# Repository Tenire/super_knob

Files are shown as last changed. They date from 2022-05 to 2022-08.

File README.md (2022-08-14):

# Super knob

## 介绍
Super knob 是基于ESP32与无刷电机实现的超级旋钮，该项目基于国外开源项目：[smartknob](https://github.com/scottbez1/smartknob)

我将无刷电机的旋钮部分解耦出来，通过磁吸的方式搭配不同的底座，来实现各种应用场景，同时设计了一套协议用于旋钮与底座的交互，可实现针对不同场景带来不同的触感体验，甚至可以在同一个场景的不同操作下模拟不同的触感和阻尼反馈。类似于智能手机中线性马达对于不同应用或页面的机械触感模拟。

同时磁吸的灵感来源于大疆的Action2 方块相机，啪，即可将旋钮与不同外设进行磁吸配对，待开发稳定后，计划用CNC加工金属的外壳，来配合磁吸达到最舒服的体验。

例如：当同一个旋钮组件，磁吸到物联网中控的底座上面，自动弹出对应的UI界面，同时可以控制智能家具，且在控制台灯亮度和空调温度的时候，会带来不同的旋钮触感反馈。

例如：当同一个旋钮组件，磁吸到PC旋钮底座上面，即可变身为PC的超级旋钮，可以用他做翻页、快捷键、切换应用、调节音量和亮度，只要你喜欢，都可以分别为这几个功能配置不同的阻尼反馈。

将旋钮部分解耦开来，搭配不同的底座，即可实现控制万物，且触感与阻尼感各不相同，这是普通的机械旋钮不能带来的！

## 目录结构

1.Firmware   固件代码 平台为platformIO

2.Hardware  硬件PCB相关文件

3.Model  三维模型文件，软件为SolidWorks

4.Super Knob Submodules 超级旋钮底座子模块，或许会增加更多

Docs 图片资源

Tools 字库等工具

## 设计草图

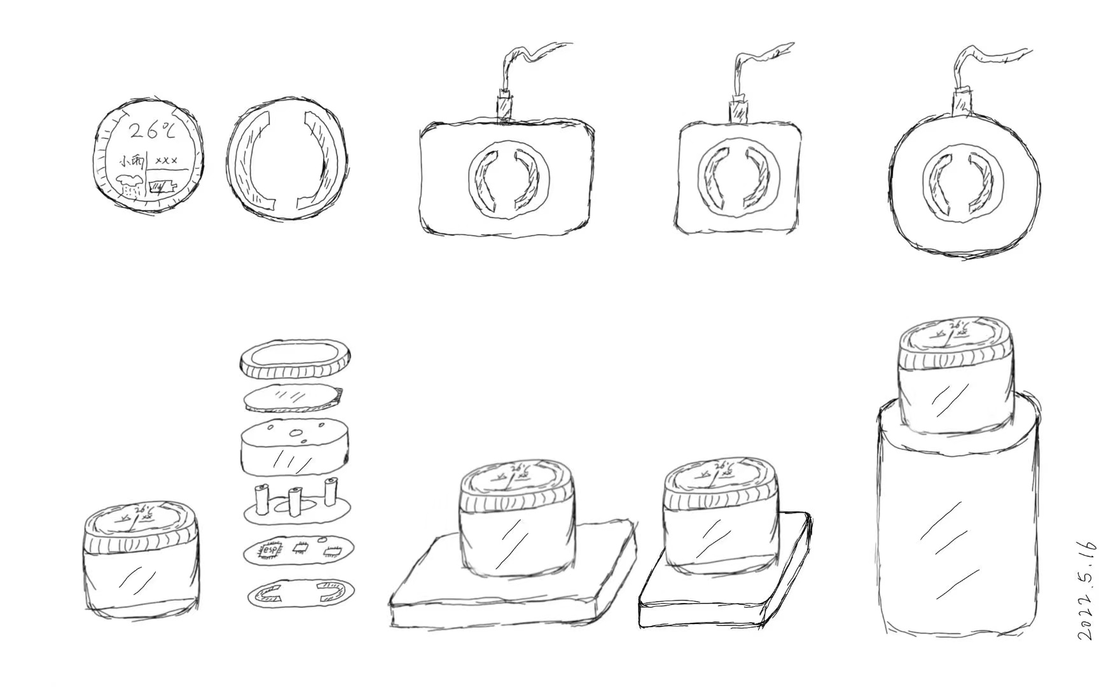
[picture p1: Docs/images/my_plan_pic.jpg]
my_plan_pic


## 功能架构

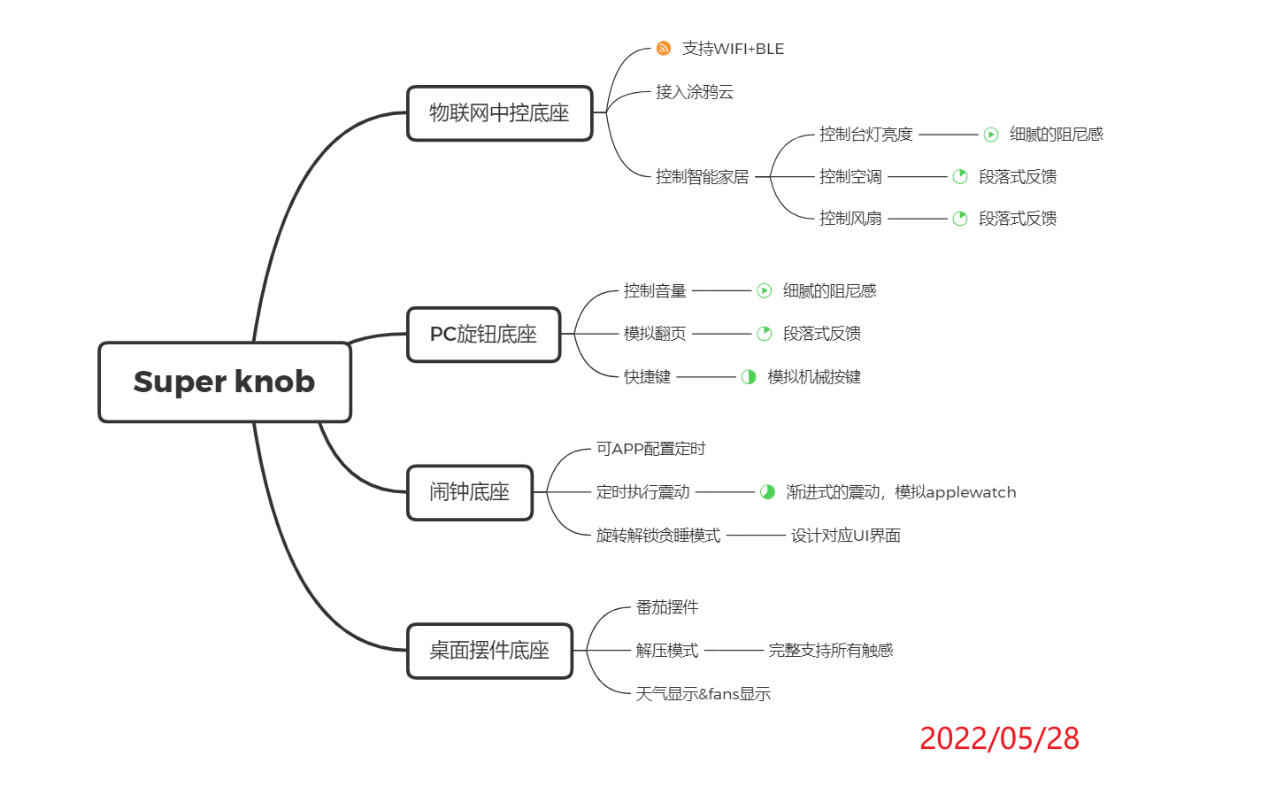
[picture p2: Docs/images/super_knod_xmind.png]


## UI界面演示

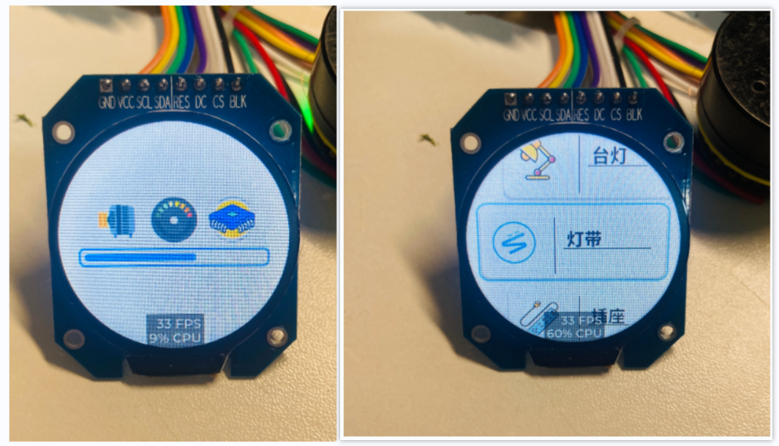
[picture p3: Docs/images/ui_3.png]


## 3D模型（初版）

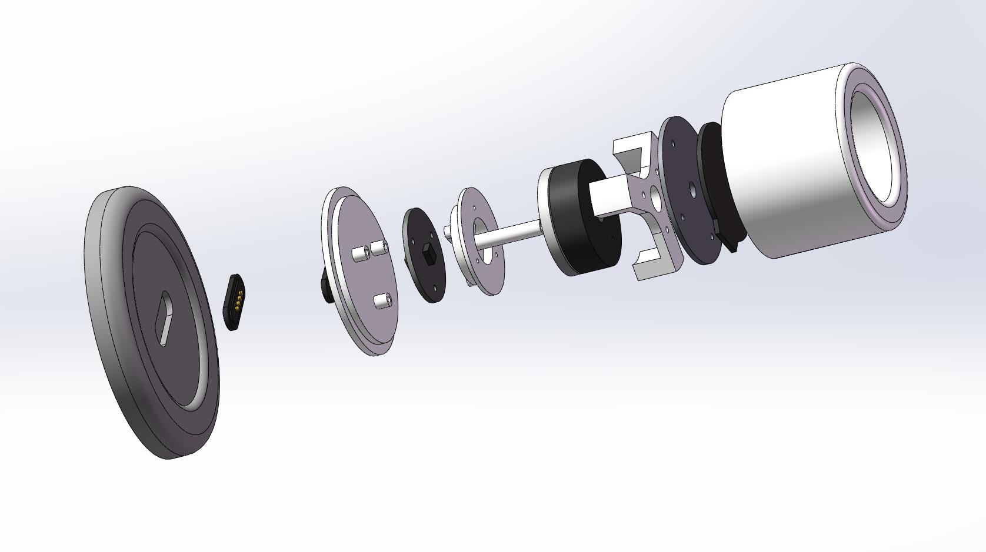
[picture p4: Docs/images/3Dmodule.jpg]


改进版本：

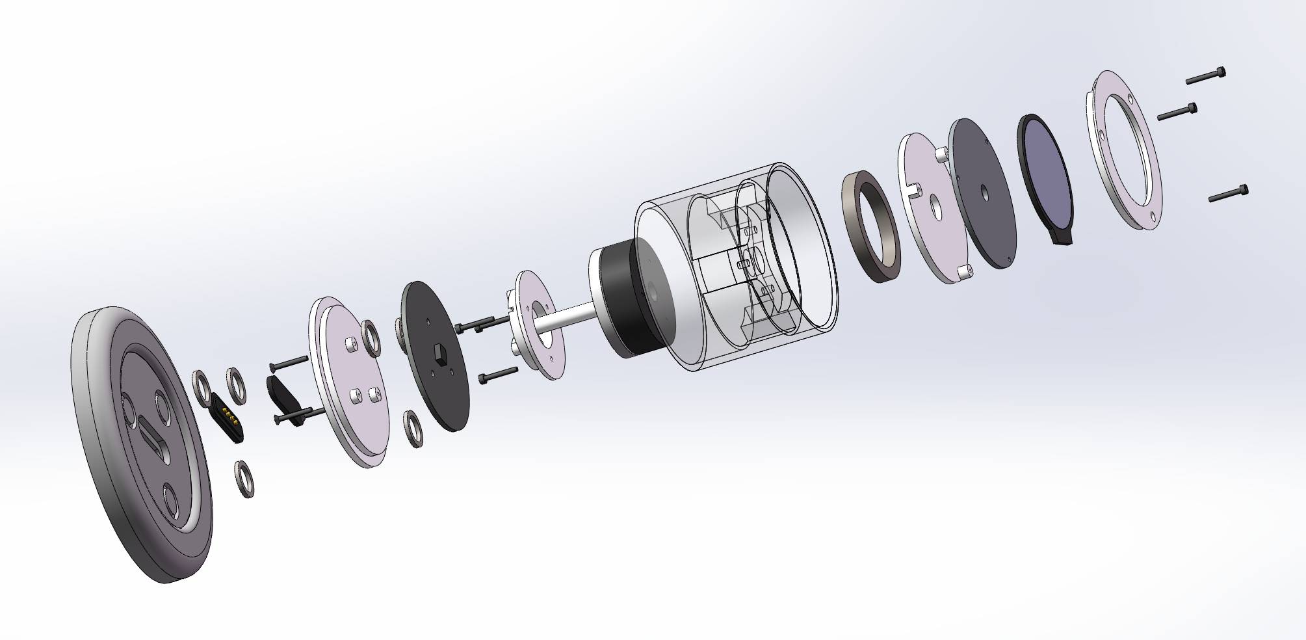
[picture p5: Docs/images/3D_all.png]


兼容2804电机：

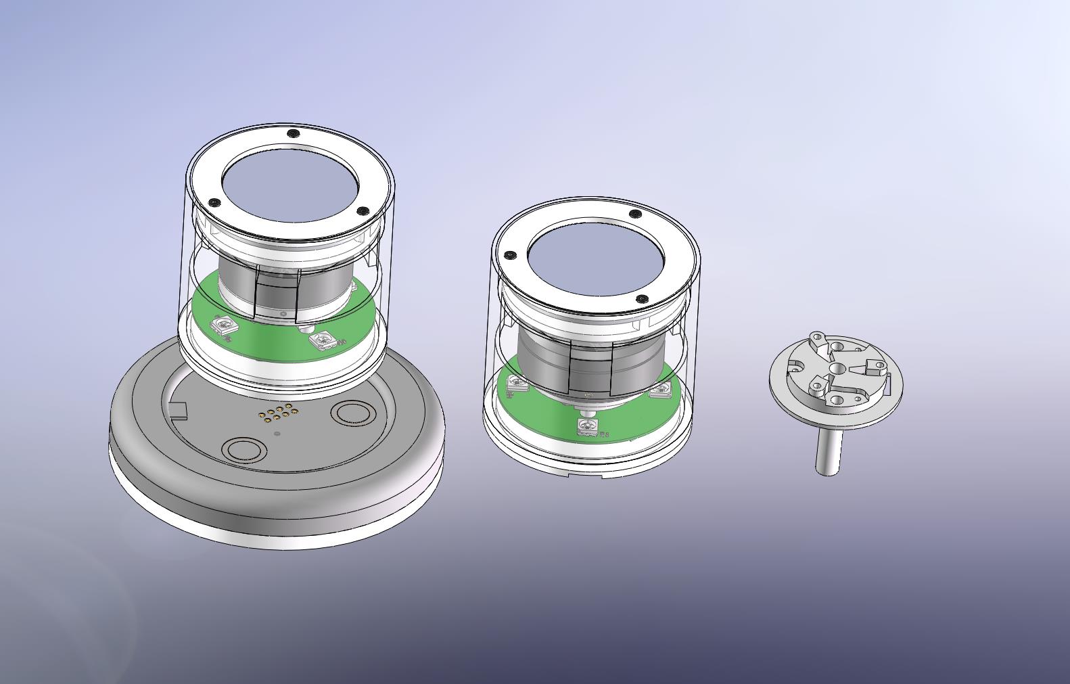
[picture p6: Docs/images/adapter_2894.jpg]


# Super knob Lite

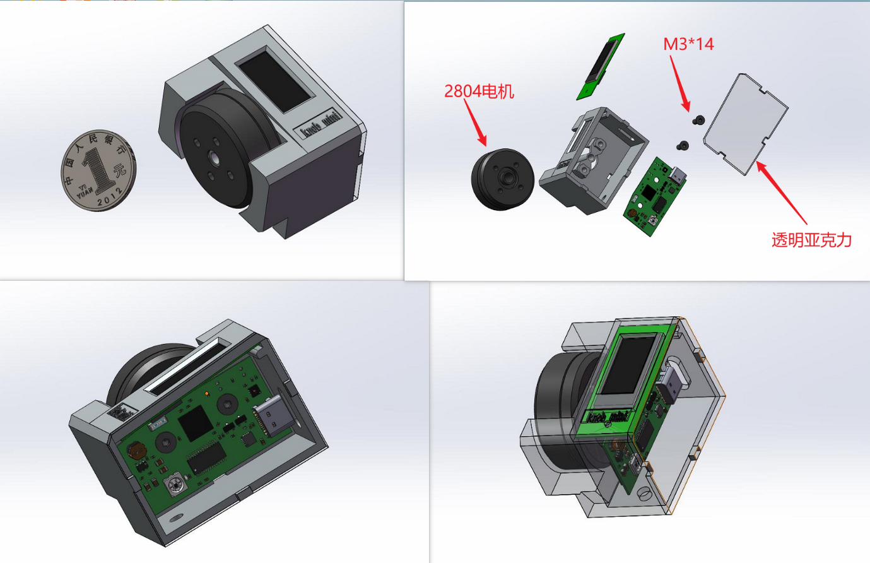
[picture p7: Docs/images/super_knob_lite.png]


## 介绍

Super knob Lite 是基于Super knob的版本进行了优化缩小的 迷你版本，整体外观是参考稚晖君键盘左侧拓展模块设计而来，当天看到稚晖君发布视频后，我拿起游标卡尺和电机就开始了设计，几个小时完成并连夜画PCB验证，并且一次打样通过！致敬偶像，一直激励着我们学习新的东西。

固件代码请切换至 develop/super_knob_lite分支 我还在持续优化ing

`git fetch`

`git pull`

`git checkout  develop/super_knob_lite`

## 电机选型

该项目已适配2804电机，能正常买到，目前看来供货充足，同时也需要配一个径向磁铁磁环

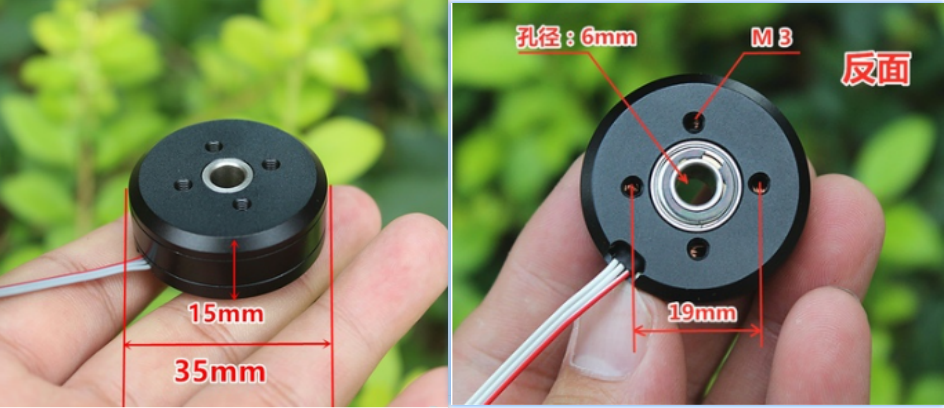
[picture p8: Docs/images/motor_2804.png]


2804电机淘宝链接：[链接地址](https://item.taobao.com/item.htm?spm=a1z09.2.0.0.10d92e8d2bksqC&id=656316178382&_u=22es8v8793db)

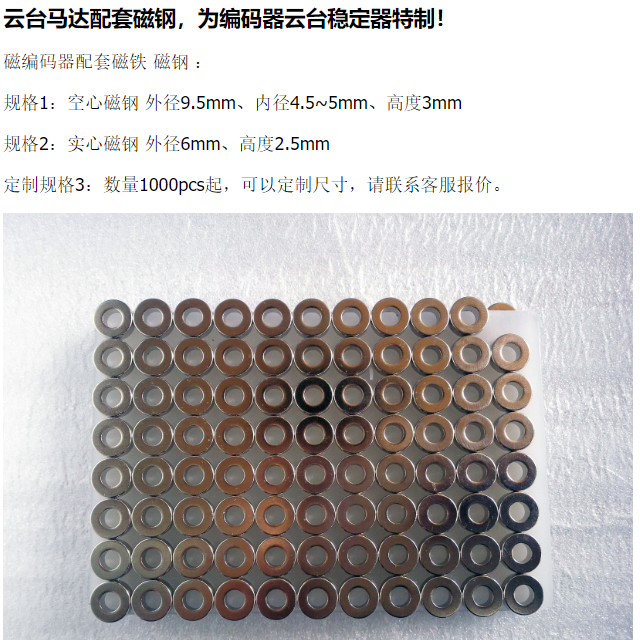
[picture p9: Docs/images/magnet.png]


径向磁铁淘宝链接：[链接地址](https://item.taobao.com/item.htm?spm=a1z09.2.0.0.1a622e8d9RsXzr&id=547732283636&_u=e2es8v87891e)

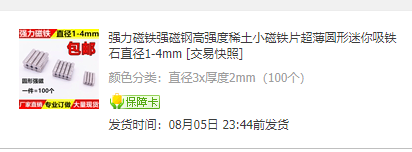
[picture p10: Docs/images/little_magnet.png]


亚克力外壳磁吸 小磁铁(直径3 厚度2)：[链接地址](https://item.taobao.com/item.htm?spm=a1z09.2.0.0.1a622e8d9RsXzr&id=536670444365&_u=e2es8v878c66)

关于左侧的按键，其实是通过ESP32的TouchGPIO来实现的，从PCB引出GPIO贯穿电机到达左侧，手指触摸即可得到相应反馈，同时电机也会模拟震动，来达到机械按键的效果。

## 视频演示：

功能演示：
https://www.bilibili.com/video/BV1GG4y1q7WF

详细介绍与开发指导：
https://www.bilibili.com/video/BV1BB4y157gH

# 鸣谢

https://github.com/peng-zhihui/HelloWord-Keyboard

https://github.com/scottbez1/smartknob

https://github.com/ToanTech/Deng-s-foc-controller

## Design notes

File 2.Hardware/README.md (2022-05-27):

<!--
 * @Descripttion: 
 * @version: 
 * @Author: congsir
 * @Date: 2022-05-26 23:58:26
 * @LastEditors: 
 * @LastEditTime: 2022-05-27 23:52:37
-->
# Super knob

#### 介绍
uper knob 是基于ESP32与无刷电机实现的超级旋钮，该项目基于国外开源项目：[smartknob](https://github.com/scottbez1/smartknob)

my_plan_pic

ui_1

#### 软件架构

软件架构说明

#### 安装教程

1.  xxxx
2.  xxxx
3.  xxxx

#### 使用说明

1.  xxxx
2.  xxxx
3.  xxxx

#### 参与贡献

1.  Fork 本仓库
2.  新建 Feat_xxx 分支
3.  提交代码
4.  新建 Pull Request

#### 特技

1.  使用 Readme\_XXX.md 来支持不同的语言，例如 Readme\_en.md, Readme\_zh.md
2.  Gitee 官方博客 [blog.gitee.com](https://blog.gitee.com)
3.  你可以 [https://gitee.com/explore](https://gitee.com/explore) 这个地址来了解 Gitee 上的优秀开源项目
4.  [GVP](https://gitee.com/gvp) 全称是 Gitee 最有价值开源项目，是综合评定出的优秀开源项目
5.  Gitee 官方提供的使用手册 [https://gitee.com/help](https://gitee.com/help)
6.  Gitee 封面人物是一档用来展示 Gitee 会员风采的栏目 [https://gitee.com/gitee-stars/](https://gitee.com/gitee-stars/)

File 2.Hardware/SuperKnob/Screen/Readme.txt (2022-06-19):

注：三个触摸按键的金属化过孔需要开窗。

嘉立创下单Gerber文件才能按照设计文件选择金属化过孔是否开窗。

请屏幕的PCB板按照Gerber在嘉立创下单。

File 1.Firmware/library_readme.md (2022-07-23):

<!--
 * @Descripttion: 
 * @version: 
 * @Author: congsir
 * @Date: 2022-05-22 23:52:31
 * @LastEditors: wenzheng 565402462@qq.com
 * @LastEditTime: 2022-07-23 16:10:56
-->
## 依赖库的配置与注意事项

simple FOC 的版本2.2.1→ ESP32版本4.1.0！！！！！！！！

1 TFT_eSPI/User_Setup.h

2 lvgl/lv_conf.h

---

TFT_eSPI/User_Setup.h
```

#define GC9A01_DRIVER

//#define ST7789_DRIVER  
#define TFT_WIDTH  240
#define TFT_HEIGHT 240

#ifdef ESP32C3_ENABLE
    #define TFT_MOSI 3 // In some display driver board, it might be written as "SDA" and so on.15
    #define TFT_SCLK 2 //14
    #define TFT_CS   7  // Chip select control pin
    #define TFT_DC   6  // Data Command control pin
    #define TFT_RST  10  // Reset pin (could connect to Arduino RESET pin)
    #define TFT_BL   12  // LED back-light
#else
    #define TFT_MOSI 13 // In some display driver board, it might be written as "SDA" and so on.15
    #define TFT_SCLK 14 //14
    #define TFT_CS   15  // Chip select control pin
    #define TFT_DC   27  // Data Command control pin
    #define TFT_RST  2  // Reset pin (could connect to Arduino RESET pin)
    #define TFT_BL   12  // LED back-light
    #define ESP32_DMA
#endif // ESP32C3_ENABLE

#define LOAD_GLCD   // Font 1. Original Adafruit 8 pixel font needs ~1820 bytes in FLASH
// #define LOAD_FONT2  // Font 2. Small 16 pixel high font, needs ~3534 bytes in FLASH, 96 characters
// #define LOAD_FONT4  // Font 4. Medium 26 pixel high font, needs ~5848 bytes in FLASH, 96 characters
// #define LOAD_FONT6  // Font 6. Large 48 pixel font, needs ~2666 bytes in FLASH, only characters 1234567890:-.apm
// #define LOAD_FONT7  // Font 7. 7 segment 48 pixel font, needs ~2438 bytes in FLASH, only characters 1234567890:-.
// #define LOAD_FONT8  // Font 8. Large 75 pixel font needs ~3256 bytes in FLASH, only characters 1234567890:-.
// #define LOAD_GFXFF  // FreeFonts. Include access to the 48 Adafruit_GFX free fonts FF1 to FF48 and custom fonts

//#define SMOOTH_FONT
#define SPI_FREQUENCY  80000000
#define SPI_READ_FREQUENCY  8000000
//#define SPI_TOUCH_FREQUENCY  2500000 

//https://www.bilibili.com/read/cv13270143?spm_id_from=333.999.0.0

```
lvgl/lv_conf.h

```
/**
 * @file lv_conf.h
 * Configuration file for v8.2.0
 */

/*
 * Copy this file as `lv_conf.h`
 * 1. simply next to the `lvgl` folder
 * 2. or any other places and
 *    - define `LV_CONF_INCLUDE_SIMPLE`
 *    - add the path as include path
 */

/* clang-format off */
#if 1 /*Set it to "1" to enable content*/

#ifndef LV_CONF_H
#define LV_CONF_H

#include <stdint.h>

/*====================
   COLOR SETTINGS
 *====================*/

/*Color depth: 1 (1 byte per pixel), 8 (RGB332), 16 (RGB565), 32 (ARGB8888)*/
#define LV_COLOR_DEPTH 16

/*Swap the 2 bytes of RGB565 color. Useful if the display has an 8-bit interface (e.g. SPI)*/
#define LV_COLOR_16_SWAP 0

/*Enable more complex drawing routines to manage screens transparency.
 *Can be used if the UI is above another layer, e.g. an OSD menu or video player.
 *Requires `LV_COLOR_DEPTH = 32` colors and the screen's `bg_opa` should be set to non LV_OPA_COVER value*/
#define LV_COLOR_SCREEN_TRANSP 0

/* Adjust color mix functions rounding. GPUs might calculate color mix (blending) differently.
 * 0: round down, 64: round up from x.75, 128: round up from half, 192: round up from x.25, 254: round up */
#define LV_COLOR_MIX_ROUND_OFS (LV_COLOR_DEPTH == 32 ? 0: 128)

/*Images pixels with this color will not be drawn if they are chroma keyed)*/
#define LV_COLOR_CHROMA_KEY lv_color_hex(0x00ff00)         /*pure green*/

/*=========================
   MEMORY SETTINGS
 *=========================*/

/*1: use custom malloc/free, 0: use the built-in `lv_mem_alloc()` and `lv_mem_free()`*/
#define LV_MEM_CUSTOM 0
#if LV_MEM_CUSTOM == 0
    /*Size of the memory available for `lv_mem_alloc()` in bytes (>= 2kB)*/
    #define LV_MEM_SIZE (64U * 1024U)          /*[bytes]*/

    /*Set an address for the memory pool instead of allocating it as a normal array. Can be in external SRAM too.*/
    #define LV_MEM_ADR 0     /*0: unused*/
    /*Instead of an address give a memory allocator that will be called to get a memory pool for LVGL. E.g. my_malloc*/
    #if LV_MEM_ADR == 0
        //#define LV_MEM_POOL_INCLUDE your_alloc_library  /* Uncomment if using an external allocator*/
        //#define LV_MEM_POOL_ALLOC   your_alloc          /* Uncomment if using an external allocator*/
    #endif

#else       /*LV_MEM_CUSTOM*/
    #define LV_MEM_CUSTOM_INCLUDE <stdlib.h>   /*Header for the dynamic memory function*/
    #define LV_MEM_CUSTOM_ALLOC   malloc
    #define LV_MEM_CUSTOM_FREE    free
    #define LV_MEM_CUSTOM_REALLOC realloc
#endif     /*LV_MEM_CUSTOM*/

/*Number of the intermediate memory buffer used during rendering and other internal processing mechanisms.
 *You will see an error log message if there wasn't enough buffers. */
#define LV_MEM_BUF_MAX_NUM 16

/*Use the standard `memcpy` and `memset` instead of LVGL's own functions. (Might or might not be faster).*/
#define LV_MEMCPY_MEMSET_STD 0

/*====================
   HAL SETTINGS
 *====================*/

/*Default display refresh period. LVG will redraw changed areas with this period time*/
#define LV_DISP_DEF_REFR_PERIOD 30      /*[ms]*/

/*Input device read period in milliseconds*/
#define LV_INDEV_DEF_READ_PERIOD 30     /*[ms]*/

/*Use a custom tick source that tells the elapsed time in milliseconds.
 *It removes the need to manually update the tick with `lv_tick_inc()`)*/
#define LV_TICK_CUSTOM 1
#if LV_TICK_CUSTOM
    #define LV_TICK_CUSTOM_INCLUDE "Arduino.h"         /*Header for the system time function*/
    #define LV_TICK_CUSTOM_SYS_TIME_EXPR (millis())    /*Expression evaluating to current system time in ms*/
#endif   /*LV_TICK_CUSTOM*/

/*Default Dot Per Inch. Used to initialize default sizes such as widgets sized, style paddings.
 *(Not so important, you can adjust it to modify default sizes and spaces)*/
#define LV_DPI_DEF 130     /*[px/inch]*/

/*=======================
 * FEATURE CONFIGURATION
 *=======================*/

/*-------------
 * Drawing
 *-----------*/

/*Enable complex draw engine.
 *Required to draw shadow, gradient, rounded corners, circles, arc, skew lines, image transformations or any masks*/
#define LV_DRAW_COMPLEX 1
#if LV_DRAW_COMPLEX != 0

    /*Allow buffering some shadow calculation.
    *LV_SHADOW_CACHE_SIZE is the max. shadow size to buffer, where shadow size is `shadow_width + radius`
    *Caching has LV_SHADOW_CACHE_SIZE^2 RAM cost*/
    #define LV_SHADOW_CACHE_SIZE 0

    /* Set number of maximally cached circle data.
    * The circumference of 1/4 circle are saved for anti-aliasing
    * radius * 4 bytes are used per circle (the most often used radiuses are saved)
    * 0: to disable caching */
    #define LV_CIRCLE_CACHE_SIZE 4
#endif /*LV_DRAW_COMPLEX*/

/*Default image cache size. Image caching keeps the images opened.
 *If only the built-in image formats are used there is no real advantage of caching. (I.e. if no new image decoder is added)
 *With complex image decoders (e.g. PNG or JPG) caching can save the continuous open/decode of images.
 *However the opened images might consume additional RAM.
 *0: to disable caching*/
#define LV_IMG_CACHE_DEF_SIZE   0

/*Number of stops allowed per gradient. Increase this to allow more stops.
 *This adds (sizeof(lv_color_t) + 1) bytes per additional stop*/
#define LV_GRADIENT_MAX_STOPS       2

/*Default gradient buffer size.
 *When LVGL calculates the gradient "maps" it can save them into a cache to avoid calculating them again.
 *LV_GRAD_CACHE_DEF_SIZE sets the size of this cache in bytes.
 *If the cache is too small the map will be allocated only while it's required for the drawing.
 *0 mean no caching.*/
#define LV_GRAD_CACHE_DEF_SIZE      0

/*Allow dithering the gradients (to achieve visual smooth color gradients on limited color depth display)
 *LV_DITHER_GRADIENT implies allocating one or two more lines of the object's rendering surface
 *The increase in memory consumption is (32 bits * object width) plus 24 bits * object width if using error diffusion */
#define LV_DITHER_GRADIENT      0
#if LV_DITHER_GRADIENT
    /*Add support for error diffusion dithering.
     *Error diffusion dithering gets a much better visual result, but implies more CPU consumption and memory when drawing.
     *The increase in memory consumption is (24 bits * object's width)*/
    #define LV_DITHER_ERROR_DIFFUSION   0
#endif

/*Maximum buffer size to allocate for rotation.
 *Only used if software rotation is enabled in the display driver.*/
#define LV_DISP_ROT_MAX_BUF (10*1024)

/*-------------
 * GPU
 *-----------*/

/*Use STM32's DMA2D (aka Chrom Art) GPU*/
#define LV_USE_GPU_STM32_DMA2D 0
#if LV_USE_GPU_STM32_DMA2D
    /*Must be defined to include path of CMSIS header of target processor
    e.g. "stm32f769xx.h" or "stm32f429xx.h"*/
    #define LV_GPU_DMA2D_CMSIS_INCLUDE
#endif

/*Use NXP's PXP GPU iMX RTxxx platforms*/
#define LV_USE_GPU_NXP_PXP 0
#if LV_USE_GPU_NXP_PXP
    /*1: Add default bare metal and FreeRTOS interrupt handling routines for PXP (lv_gpu_nxp_pxp_osa.c)
    *   and call lv_gpu_nxp_pxp_init() automatically during lv_init(). Note that symbol SDK_OS_FREE_RTOS
    *   has to be defined in order to use FreeRTOS OSA, otherwise bare-metal implementation is selected.
    *0: lv_gpu_nxp_pxp_init() has to be called manually before lv_init()
    */
    #define LV_USE_GPU_NXP_PXP_AUTO_INIT 0
#endif

/*Use NXP's VG-Lite GPU iMX RTxxx platforms*/
#define LV_USE_GPU_NXP_VG_LITE 0

/*Use SDL renderer API*/
#define LV_USE_GPU_SDL 0
#if LV_USE_GPU_SDL
    #define LV_GPU_SDL_INCLUDE_PATH <SDL2/SDL.h>
    /*Texture cache size, 8MB by default*/
    #define LV_GPU_SDL_LRU_SIZE (1024 * 1024 * 8)
    /*Custom blend mode for mask drawing, disable if you need to link with older SDL2 lib*/
    #define LV_GPU_SDL_CUSTOM_BLEND_MODE (SDL_VERSION_ATLEAST(2, 0, 6))
#endif

/*-------------
 * Logging
 *-----------*/

/*Enable the log module*/
#define LV_USE_LOG 0
#if LV_USE_LOG

    /*How important log should be added:
    *LV_LOG_LEVEL_TRACE       A lot of logs to give detailed information
    *LV_LOG_LEVEL_INFO        Log important events
    *LV_LOG_LEVEL_WARN        Log if something unwanted happened but didn't cause a problem
    *LV_LOG_LEVEL_ERROR       Only critical issue, when the system may fail
    *LV_LOG_LEVEL_USER        Only logs added by the user
    *LV_LOG_LEVEL_NONE        Do not log anything*/
    #define LV_LOG_LEVEL LV_LOG_LEVEL_WARN

    /*1: Print the log with 'printf';
    *0: User need to register a callback with `lv_log_register_print_cb()`*/
    #define LV_LOG_PRINTF 0

    /*Enable/disable LV_LOG_TRACE in modules that produces a huge number of logs*/
    #define LV_LOG_TRACE_MEM        1
    #define LV_LOG_TRACE_TIMER      1
    #define LV_LOG_TRACE_INDEV      1
    #define LV_LOG_TRACE_DISP_REFR  1
    #define LV_LOG_TRACE_EVENT      1
    #define LV_LOG_TRACE_OBJ_CREATE 1
    #define LV_LOG_TRACE_LAYOUT     1
    #define LV_LOG_TRACE_ANIM       1

#endif  /*LV_USE_LOG*/

/*-------------
 * Asserts
 *-----------*/

/*Enable asserts if an operation is failed or an invalid data is found.
 *If LV_USE_LOG is enabled an error message will be printed on failure*/
#define LV_USE_ASSERT_NULL          1   /*Check if the parameter is NULL. (Very fast, recommended)*/
#define LV_USE_ASSERT_MALLOC        1   /*Checks is the memory is successfully allocated or no. (Very fast, recommended)*/
#define LV_USE_ASSERT_STYLE         0   /*Check if the styles are properly initialized. (Very fast, recommended)*/
#define LV_USE_ASSERT_MEM_INTEGRITY 0   /*Check the integrity of `lv_mem` after critical operations. (Slow)*/
#define LV_USE_ASSERT_OBJ           0   /*Check the object's type and existence (e.g. not deleted). (Slow)*/

/*Add a custom handler when assert happens e.g. to restart the MCU*/
#define LV_ASSERT_HANDLER_INCLUDE <stdint.h>
#define LV_ASSERT_HANDLER while(1);   /*Halt by default*/

/*-------------
 * Others
 *-----------*/

/*1: Show CPU usage and FPS count*/
#define LV_USE_PERF_MONITOR 1
#if LV_USE_PERF_MONITOR
    #define LV_USE_PERF_MONITOR_POS LV_ALIGN_BOTTOM_MID
#endif

/*1: Show the used memory and the memory fragmentation
 * Requires LV_MEM_CUSTOM = 0*/
#define LV_USE_MEM_MONITOR 0
#if LV_USE_MEM_MONITOR
    #define LV_USE_MEM_MONITOR_POS LV_ALIGN_BOTTOM_LEFT
#endif

/*1: Draw random colored rectangles over the redrawn areas*/
#define LV_USE_REFR_DEBUG 0

/*Change the built in (v)snprintf functions*/
#define LV_SPRINTF_CUSTOM 0
#if LV_SPRINTF_CUSTOM
    #define LV_SPRINTF_INCLUDE <stdio.h>
    #define lv_snprintf  snprintf
    #define lv_vsnprintf vsnprintf
#else   /*LV_SPRINTF_CUSTOM*/
    #define LV_SPRINTF_USE_FLOAT 0
#endif  /*LV_SPRINTF_CUSTOM*/

#define LV_USE_USER_DATA 1

/*Garbage Collector settings
 *Used if lvgl is bound to higher level language and the memory is managed by that language*/
#define LV_ENABLE_GC 0
#if LV_ENABLE_GC != 0
    #define LV_GC_INCLUDE "gc.h"                           /*Include Garbage Collector related things*/
#endif /*LV_ENABLE_GC*/

/*=====================
 *  COMPILER SETTINGS
 *====================*/

/*For big endian systems set to 1*/
#define LV_BIG_ENDIAN_SYSTEM 0

/*Define a custom attribute to `lv_tick_inc` function*/
#define LV_ATTRIBUTE_TICK_INC

/*Define a custom attribute to `lv_timer_handler` function*/
#define LV_ATTRIBUTE_TIMER_HANDLER

/*Define a custom attribute to `lv_disp_flush_ready` function*/
#define LV_ATTRIBUTE_FLUSH_READY

/*Required alignment size for buffers*/
#define LV_ATTRIBUTE_MEM_ALIGN_SIZE 1

/*Will be added where memories needs to be aligned (with -Os data might not be aligned to boundary by default).
 * E.g. __attribute__((aligned(4)))*/
#define LV_ATTRIBUTE_MEM_ALIGN

/*Attribute to mark large constant arrays for example font's bitmaps*/
#define LV_ATTRIBUTE_LARGE_CONST

/*Compiler prefix for a big array declaration in RAM*/
#define LV_ATTRIBUTE_LARGE_RAM_ARRAY

/*Place performance critical functions into a faster memory (e.g RAM)*/
#define LV_ATTRIBUTE_FAST_MEM

/*Prefix variables that are used in GPU accelerated operations, often these need to be placed in RAM sections that are DMA accessible*/
#define LV_ATTRIBUTE_DMA

/*Export integer constant to binding. This macro is used with constants in the form of LV_<CONST> that
 *should also appear on LVGL binding API such as Micropython.*/
#define LV_EXPORT_CONST_INT(int_value) struct _silence_gcc_warning /*The default value just prevents GCC warning*/

/*Extend the default -32k..32k coordinate range to -4M..4M by using int32_t for coordinates instead of int16_t*/
#define LV_USE_LARGE_COORD 0

/*==================
 *   FONT USAGE
 *===================*/

/*Montserrat fonts with ASCII range and some symbols using bpp = 4
 *https://fonts.google.com/specimen/Montserrat*/
#define LV_FONT_MONTSERRAT_8  0
#define LV_FONT_MONTSERRAT_10 0
#define LV_FONT_MONTSERRAT_12 0
#define LV_FONT_MONTSERRAT_14 1
#define LV_FONT_MONTSERRAT_16 0
#define LV_FONT_MONTSERRAT_18 0
#define LV_FONT_MONTSERRAT_20 0
#define LV_FONT_MONTSERRAT_22 0
#define LV_FONT_MONTSERRAT_24 0
#define LV_FONT_MONTSERRAT_26 0
#define LV_FONT_MONTSERRAT_28 0
#define LV_FONT_MONTSERRAT_30 0
#define LV_FONT_MONTSERRAT_32 0
#define LV_FONT_MONTSERRAT_34 0
#define LV_FONT_MONTSERRAT_36 0
#define LV_FONT_MONTSERRAT_38 0
#define LV_FONT_MONTSERRAT_40 0
#define LV_FONT_MONTSERRAT_42 0
#define LV_FONT_MONTSERRAT_44 0
#define LV_FONT_MONTSERRAT_46 0
#define LV_FONT_MONTSERRAT_48 0

/*Demonstrate special features*/
#define LV_FONT_MONTSERRAT_12_SUBPX      0
#define LV_FONT_MONTSERRAT_28_COMPRESSED 0  /*bpp = 3*/
#define LV_FONT_DEJAVU_16_PERSIAN_HEBREW 0  /*Hebrew, Arabic, Persian letters and all their forms*/
#define LV_FONT_SIMSUN_16_CJK            0  /*1000 most common CJK radicals*/

/*Pixel perfect monospace fonts*/
#define LV_FONT_UNSCII_8  0
#define LV_FONT_UNSCII_16 0

/*Optionally declare custom fonts here.
 *You can use these fonts as default font too and they will be available globally.
 *E.g. #define LV_FONT_CUSTOM_DECLARE   LV_FONT_DECLARE(my_font_1) LV_FONT_DECLARE(my_font_2)*/
#define LV_FONT_CUSTOM_DECLARE

/*Always set a default font*/
#define LV_FONT_DEFAULT &lv_font_montserrat_14

/*Enable handling large font and/or fonts with a lot of characters.
 *The limit depends on the font size, font face and bpp.
 *Compiler error will be triggered if a font needs it.*/
#define LV_FONT_FMT_TXT_LARGE 0

/*Enables/disables support for compressed fonts.*/
#define LV_USE_FONT_COMPRESSED 0

/*Enable subpixel rendering*/
#define LV_USE_FONT_SUBPX 0
#if LV_USE_FONT_SUBPX
    /*Set the pixel order of the display. Physical order of RGB channels. Doesn't matter with "normal" fonts.*/
    #define LV_FONT_SUBPX_BGR 0  /*0: RGB; 1:BGR order*/
#endif

/*=================
 *  TEXT SETTINGS
 *=================*/

/**
 * Select a character encoding for strings.
 * Your IDE or editor should have the same character encoding
 * - LV_TXT_ENC_UTF8
 * - LV_TXT_ENC_ASCII
 */
#define LV_TXT_ENC LV_TXT_ENC_UTF8

/*Can break (wrap) texts on these chars*/
#define LV_TXT_BREAK_CHARS " ,.;:-_"

/*If a word is at least this long, will break wherever "prettiest"
 *To disable, set to a value <= 0*/
#define LV_TXT_LINE_BREAK_LONG_LEN 0

/*Minimum number of characters in a long word to put on a line before a break.
 *Depends on LV_TXT_LINE_BREAK_LONG_LEN.*/
#define LV_TXT_LINE_BREAK_LONG_PRE_MIN_LEN 3

/*Minimum number of characters in a long word to put on a line after a break.
 *Depends on LV_TXT_LINE_BREAK_LONG_LEN.*/
#define LV_TXT_LINE_BREAK_LONG_POST_MIN_LEN 3

/*The control character to use for signalling text recoloring.*/
#define LV_TXT_COLOR_CMD "#"

/*Support bidirectional texts. Allows mixing Left-to-Right and Right-to-Left texts.
 *The direction will be processed according to the Unicode Bidirectional Algorithm:
 *https://www.w3.org/International/articles/inline-bidi-markup/uba-basics*/
#define LV_USE_BIDI 0
#if LV_USE_BIDI
    /*Set the default direction. Supported values:
    *`LV_BASE_DIR_LTR` Left-to-Right
    *`LV_BASE_DIR_RTL` Right-to-Left
    *`LV_BASE_DIR_AUTO` detect texts base direction*/
    #define LV_BIDI_BASE_DIR_DEF LV_BASE_DIR_AUTO
#endif

/*Enable Arabic/Persian processing
 *In these languages characters should be replaced with an other form based on their position in the text*/
#define LV_USE_ARABIC_PERSIAN_CHARS 0

/*==================
 *  WIDGET USAGE
 *================*/

/*Documentation of the widgets: https://docs.lvgl.io/latest/en/html/widgets/index.html*/

#define LV_USE_ARC        1

#define LV_USE_ANIMIMG    1

#define LV_USE_BAR        1

#define LV_USE_BTN        1

#define LV_USE_BTNMATRIX  1

#define LV_USE_CANVAS     1

#define LV_USE_CHECKBOX   1

#define LV_USE_DROPDOWN   1   /*Requires: lv_label*/

#define LV_USE_IMG        1   /*Requires: lv_label*/

#define LV_USE_LABEL      1
#if LV_USE_LABEL
    #define LV_LABEL_TEXT_SELECTION 1 /*Enable selecting text of the label*/
    #define LV_LABEL_LONG_TXT_HINT 1  /*Store some extra info in labels to speed up drawing of very long texts*/
#endif

#define LV_USE_LINE       1

#define LV_USE_ROLLER     1   /*Requires: lv_label*/
#if LV_USE_ROLLER
    #define LV_ROLLER_INF_PAGES 7 /*Number of extra "pages" when the roller is infinite*/
#endif

#define LV_USE_SLIDER     1   /*Requires: lv_bar*/

#define LV_USE_SWITCH     1

#define LV_USE_TEXTAREA   1   /*Requires: lv_label*/
#if LV_USE_TEXTAREA != 0
    #define LV_TEXTAREA_DEF_PWD_SHOW_TIME 1500    /*ms*/
#endif

#define LV_USE_TABLE      1

/*==================
 * EXTRA COMPONENTS
 *==================*/

/*-----------
 * Widgets
 *----------*/
#define LV_USE_CALENDAR   1
#if LV_USE_CALENDAR
    #define LV_CALENDAR_WEEK_STARTS_MONDAY 0
    #if LV_CALENDAR_WEEK_STARTS_MONDAY
        #define LV_CALENDAR_DEFAULT_DAY_NAMES {"Mo", "Tu", "We", "Th", "Fr", "Sa", "Su"}
    #else
        #define LV_CALENDAR_DEFAULT_DAY_NAMES {"Su", "Mo", "Tu", "We", "Th", "Fr", "Sa"}
    #endif

    #define LV_CALENDAR_DEFAULT_MONTH_NAMES {"January", "February", "March",  "April", "May",  "June", "July", "August", "September", "October", "November", "December"}
    #define LV_USE_CALENDAR_HEADER_ARROW 1
    #define LV_USE_CALENDAR_HEADER_DROPDOWN 1
#endif  /*LV_USE_CALENDAR*/

#define LV_USE_CHART      1

#define LV_USE_COLORWHEEL 1

#define LV_USE_IMGBTN     1

#define LV_USE_KEYBOARD   1

#define LV_USE_LED        1

#define LV_USE_LIST       1

#define LV_USE_MENU       1

#define LV_USE_METER      1

#define LV_USE_MSGBOX     1

#define LV_USE_SPINBOX    1

#define LV_USE_SPINNER    1

#define LV_USE_TABVIEW    1

#define LV_USE_TILEVIEW   1

#define LV_USE_WIN        1

#define LV_USE_SPAN       1
#if LV_USE_SPAN
    /*A line text can contain maximum num of span descriptor */
    #define LV_SPAN_SNIPPET_STACK_SIZE 64
#endif

/*-----------
 * Themes
 *----------*/

/*A simple, impressive and very complete theme*/
#define LV_USE_THEME_DEFAULT 1
#if LV_USE_THEME_DEFAULT

    /*0: Light mode; 1: Dark mode*/
    #define LV_THEME_DEFAULT_DARK 0

    /*1: Enable grow on press*/
    #define LV_THEME_DEFAULT_GROW 1

    /*Default transition time in [ms]*/
    #define LV_THEME_DEFAULT_TRANSITION_TIME 80
#endif /*LV_USE_THEME_DEFAULT*/

/*A very simple theme that is a good starting point for a custom theme*/
#define LV_USE_THEME_BASIC 1

/*A theme designed for monochrome displays*/
#define LV_USE_THEME_MONO 1

/*-----------
 * Layouts
 *----------*/

/*A layout similar to Flexbox in CSS.*/
#define LV_USE_FLEX 1

/*A layout similar to Grid in CSS.*/
#define LV_USE_GRID 1

/*---------------------
 * 3rd party libraries
 *--------------------*/

/*File system interfaces for common APIs */

/*API for fopen, fread, etc*/
#define LV_USE_FS_STDIO 0
#if LV_USE_FS_STDIO
    #define LV_FS_STDIO_LETTER '\0'     /*Set an upper cased letter on which the drive will accessible (e.g. 'A')*/
    #define LV_FS_STDIO_PATH ""         /*Set the working directory. File/directory paths will be appended to it.*/
    #define LV_FS_STDIO_CACHE_SIZE  0   /*>0 to cache this number of bytes in lv_fs_read()*/
#endif

/*API for open, read, etc*/
#define LV_USE_FS_POSIX 0
#if LV_USE_FS_POSIX
    #define LV_FS_POSIX_LETTER '\0'     /*Set an upper cased letter on which the drive will accessible (e.g. 'A')*/
    #define LV_FS_POSIX_PATH ""         /*Set the working directory. File/directory paths will be appended to it.*/
    #define LV_FS_POSIX_CACHE_SIZE  0   /*>0 to cache this number of bytes in lv_fs_read()*/
#endif

/*API for CreateFile, ReadFile, etc*/
#define LV_USE_FS_WIN32 0
#if LV_USE_FS_WIN32
    #define LV_FS_WIN32_LETTER  '\0'    /*Set an upper cased letter on which the drive will accessible (e.g. 'A')*/
    #define LV_FS_WIN32_PATH ""         /*Set the working directory. File/directory paths will be appended to it.*/
    #define LV_FS_WIN32_CACHE_SIZE 0    /*>0 to cache this number of bytes in lv_fs_read()*/
#endif

/*API for FATFS (needs to be added separately). Uses f_open, f_read, etc*/
#define LV_USE_FS_FATFS  0
#if LV_USE_FS_FATFS
    #define LV_FS_FATFS_LETTER '\0'     /*Set an upper cased letter on which the drive will accessible (e.g. 'A')*/
    #define LV_FS_FATFS_CACHE_SIZE 0    /*>0 to cache this number of bytes in lv_fs_read()*/
#endif

/*PNG decoder library*/
#define LV_USE_PNG 0

/*BMP decoder library*/
#define LV_USE_BMP 0

/* JPG + split JPG decoder library.
 * Split JPG is a custom format optimized for embedded systems. */
#define LV_USE_SJPG 0

/*GIF decoder library*/
#define LV_USE_GIF 0

/*QR code library*/
#define LV_USE_QRCODE 0

/*FreeType library*/
#define LV_USE_FREETYPE 0
#if LV_USE_FREETYPE
    /*Memory used by FreeType to cache characters [bytes] (-1: no caching)*/
    #define LV_FREETYPE_CACHE_SIZE (16 * 1024)
    #if LV_FREETYPE_CACHE_SIZE >= 0
        /* 1: bitmap cache use the sbit cache, 0:bitmap cache use the image cache. */
        /* sbit cache:it is much more memory efficient for small bitmaps(font size < 256) */
        /* if font size >= 256, must be configured as image cache */
        #define LV_FREETYPE_SBIT_CACHE 0
        /* Maximum number of opened FT_Face/FT_Size objects managed by this cache instance. */
        /* (0:use system defaults) */
        #define LV_FREETYPE_CACHE_FT_FACES 0
        #define LV_FREETYPE_CACHE_FT_SIZES 0
    #endif
#endif

/*Rlottie library*/
#define LV_USE_RLOTTIE 0

/*FFmpeg library for image decoding and playing videos
 *Supports all major image formats so do not enable other image decoder with it*/
#define LV_USE_FFMPEG  0
#if LV_USE_FFMPEG
    /*Dump input information to stderr*/
    #define LV_FFMPEG_AV_DUMP_FORMAT 0
#endif

/*-----------
 * Others
 *----------*/

/*1: Enable API to take snapshot for object*/
#define LV_USE_SNAPSHOT 0

/*1: Enable Monkey test*/
#define LV_USE_MONKEY   0

/*1: Enable grid navigation*/
#define LV_USE_GRIDNAV  0

/*==================
* EXAMPLES
*==================*/

/*Enable the examples to be built with the library*/
#define LV_BUILD_EXAMPLES 0

/*===================
 * DEMO USAGE
 ====================*/

/*Show some widget. It might be required to increase `LV_MEM_SIZE` */
#define LV_USE_DEMO_WIDGETS        0
#if LV_USE_DEMO_WIDGETS
#define LV_DEMO_WIDGETS_SLIDESHOW  0
#endif

/*Demonstrate the usage of encoder and keyboard*/
#define LV_USE_DEMO_KEYPAD_AND_ENCODER     0

/*Benchmark your system*/
#define LV_USE_DEMO_BENCHMARK   0

/*Stress test for LVGL*/
#define LV_USE_DEMO_STRESS      0

/*Music player demo*/
#define LV_USE_DEMO_MUSIC       0
#if LV_USE_DEMO_MUSIC
# define LV_DEMO_MUSIC_SQUARE       0
# define LV_DEMO_MUSIC_LANDSCAPE    0
# define LV_DEMO_MUSIC_ROUND        0
# define LV_DEMO_MUSIC_LARGE        0
# define LV_DEMO_MUSIC_AUTO_PLAY    0
#endif

/*--END OF LV_CONF_H--*/

#endif /*LV_CONF_H*/

#endif /*End of "Content enable"*/

```

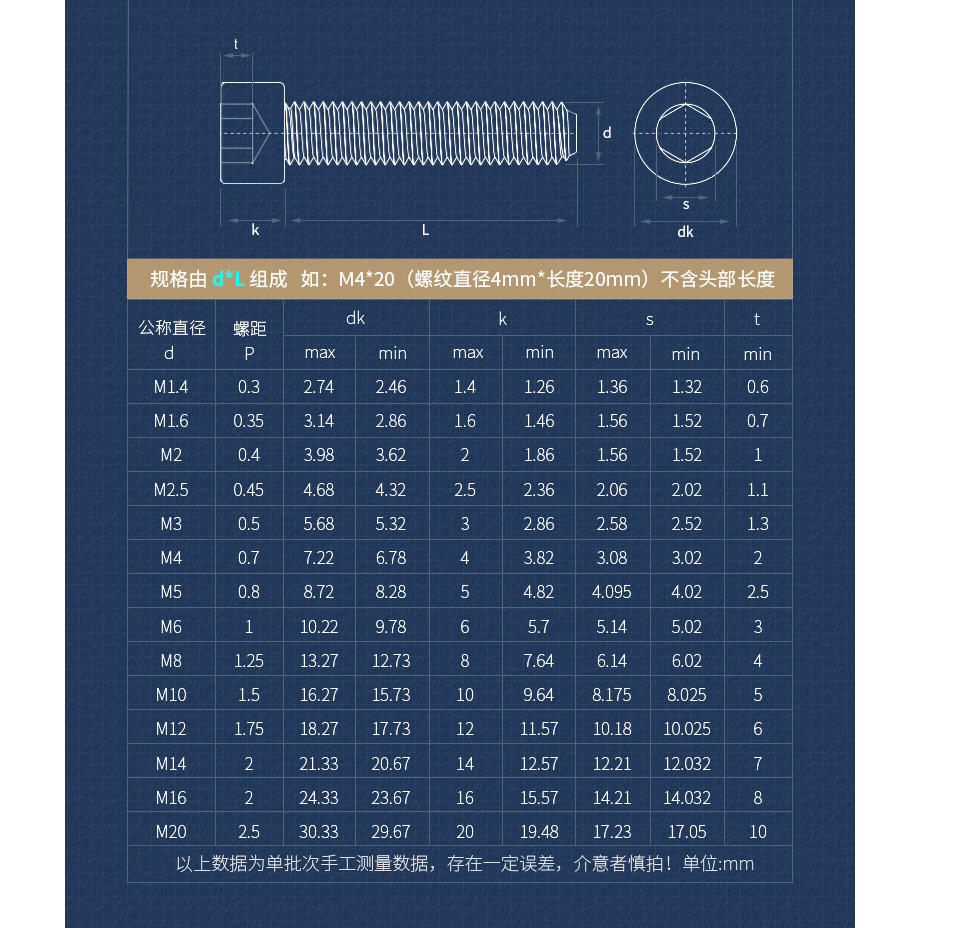
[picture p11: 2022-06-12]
3.Model/Super Knob/doc/Snipaste_2022-06-12_20-40-45.png

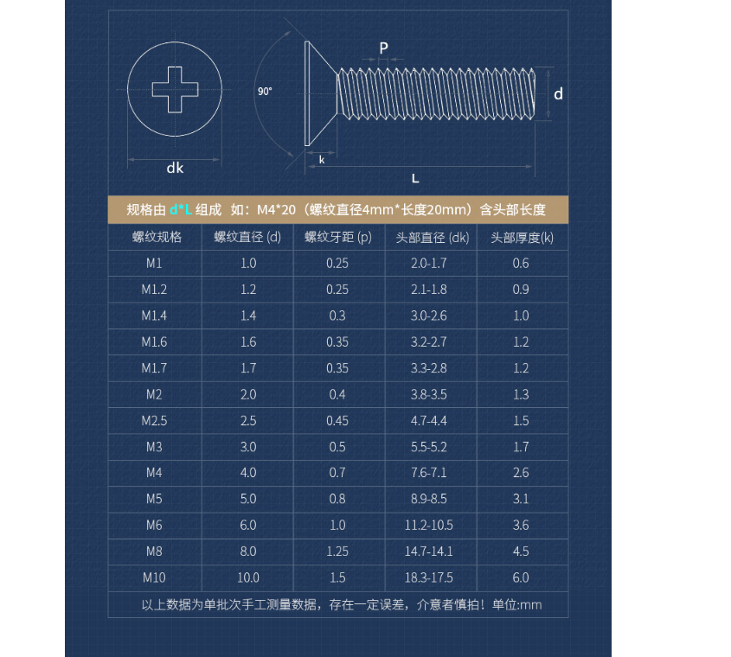
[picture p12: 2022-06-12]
3.Model/Super Knob/doc/Snipaste_2022-06-12_22-08-56.png

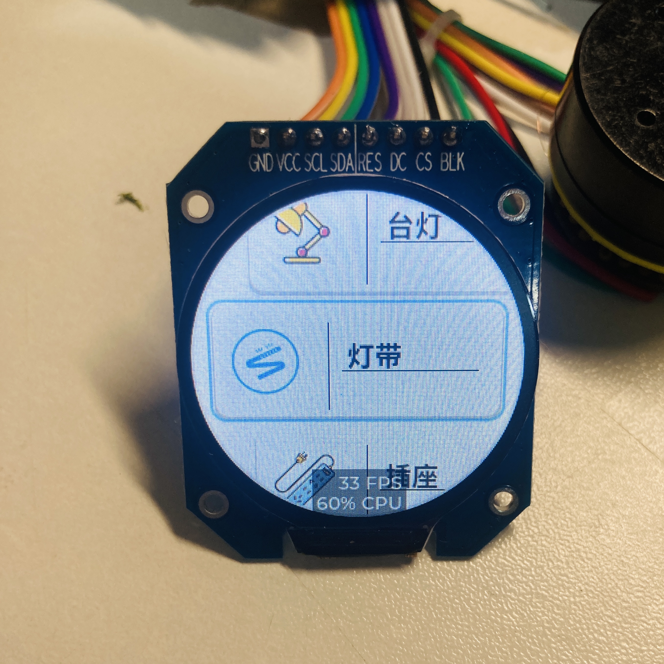
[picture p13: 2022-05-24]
Docs/images/ui_2.jpg

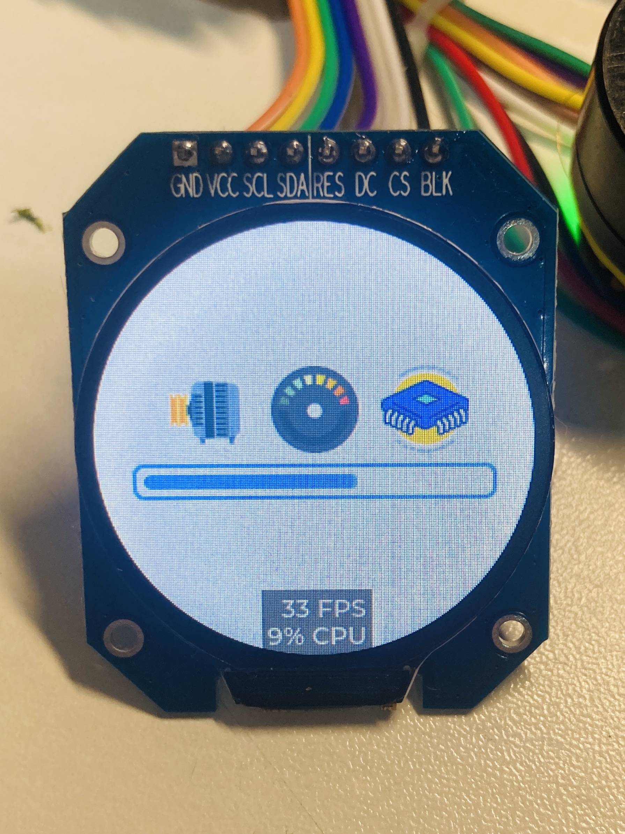
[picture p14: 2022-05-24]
Docs/images/ui_1.jpg

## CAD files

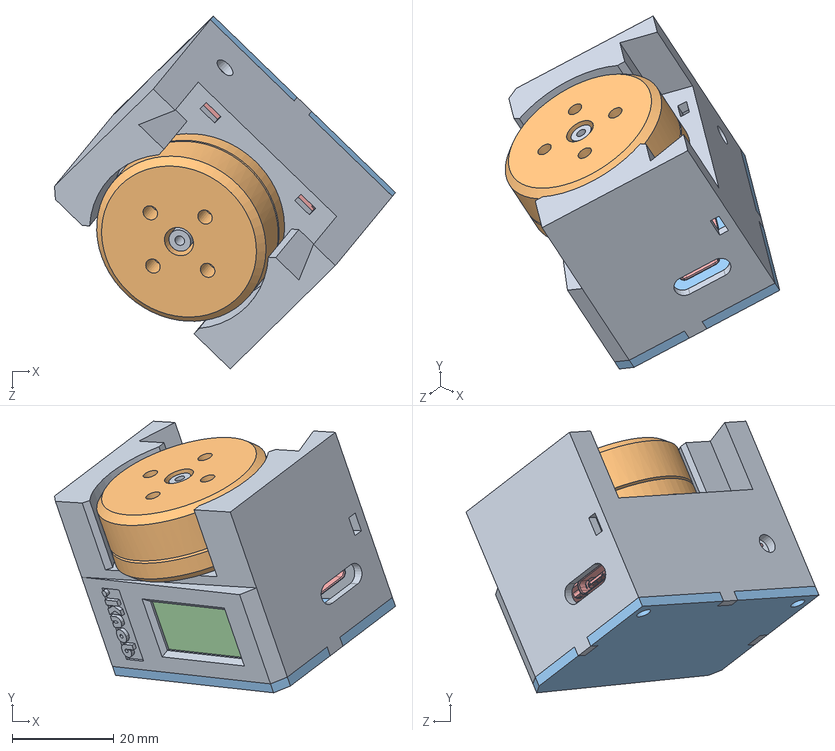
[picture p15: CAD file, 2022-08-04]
3.Model/Super Knob Lite/super knob lite.SLDASM
67.2 x 53.5 x 69.5 mm
lite_shell
motor2804
lite_shell_right
Screen_st77352
SuperKnobLite
hexagon socket countersunk head screws gb x 2

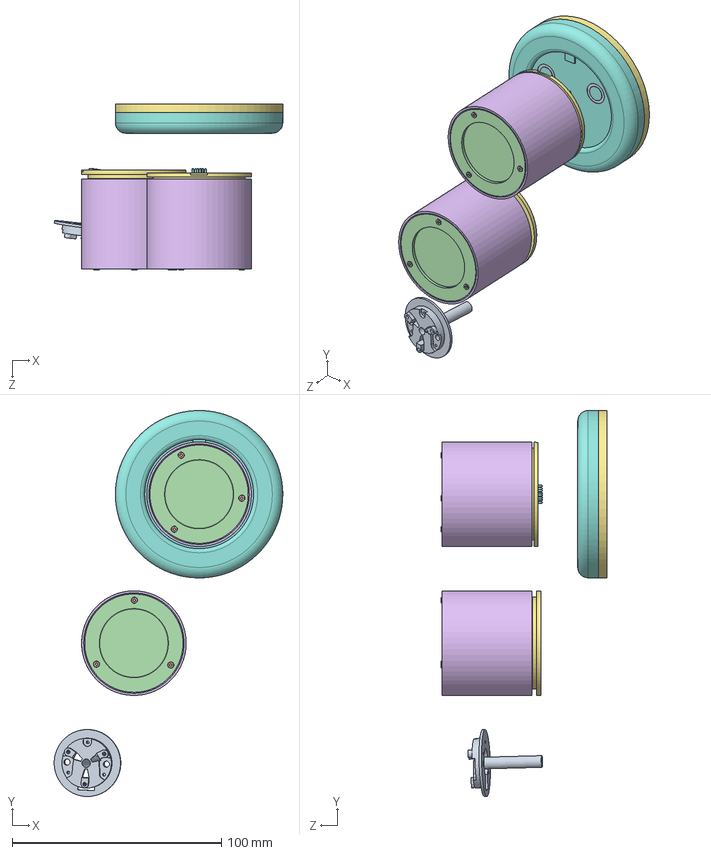
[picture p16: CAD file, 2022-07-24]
3.Model/Super Knob/SuperKnob_two_motor.SLDASM
109.2 x 184.4 x 79.3 mm
motor_base_2 x 3
motor_up
motor_down
LCD x 2
pcb_lcd x 2
motor_hold_new x 2
shell_down x 2
bottom
magnet x 6
bearing x 2
lcd_pcb_support x 2
super_knod_cap x 2
M1.4 x 6
M1.4x10_p x 3
bottom_2
pogo_pin
pogo_pin_down x 2
SuperKnob_PCB x 2
motor2804
hexagon socket button head screws gb x 2
M1.4x6 x 3
swan

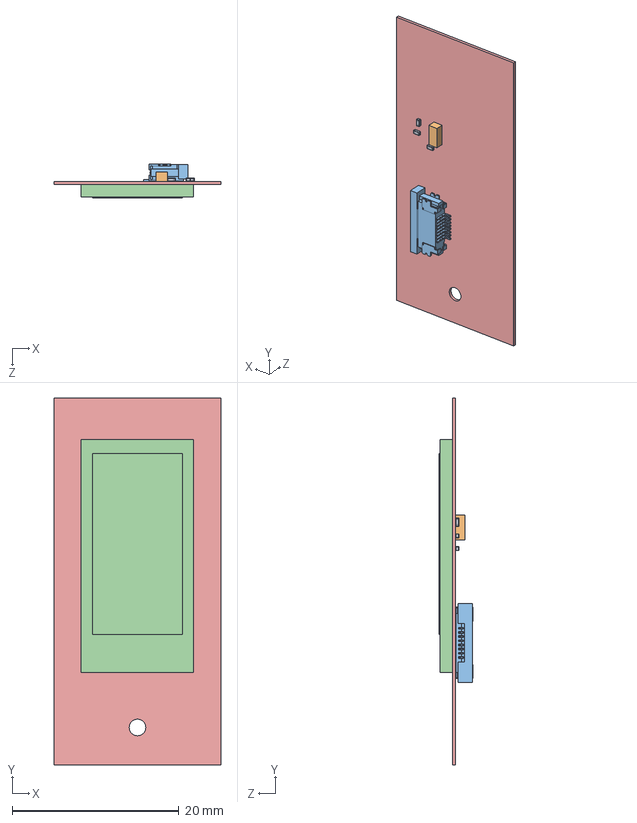
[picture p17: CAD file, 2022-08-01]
3.Model/Super Knob Lite/Screen_st7735.SLDASM
20.0 x 44.0 x 4.09 mm
RESC1005(0402).step x 3
Extruded.step
ffc_fpc_affc20-16-050-shb-t_(2).step
LCD_ST7735.step
Board.step

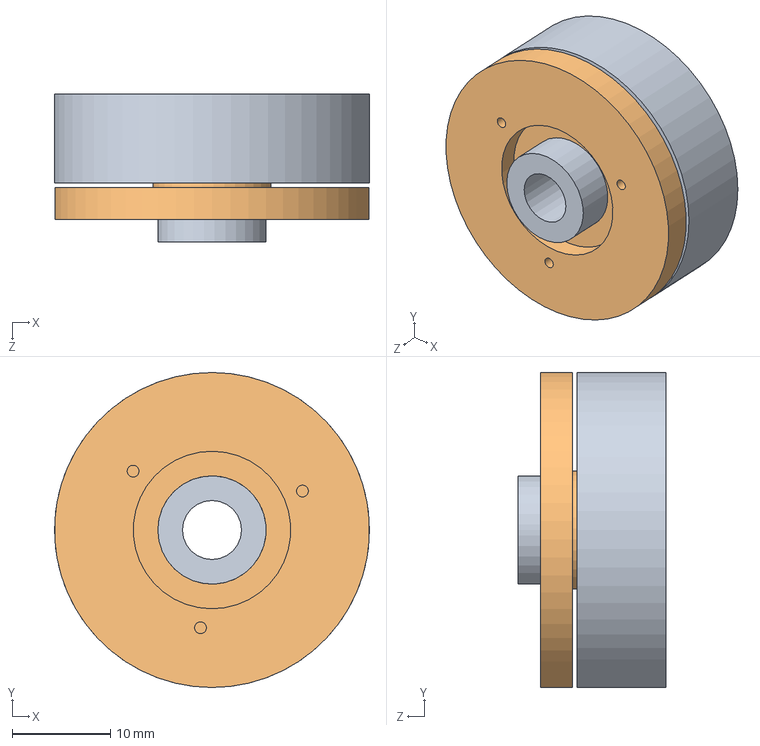
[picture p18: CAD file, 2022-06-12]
3.Model/Super Knob/motor.SLDASM
32.0 x 32.0 x 15.0 mm
motor_up
motor_down

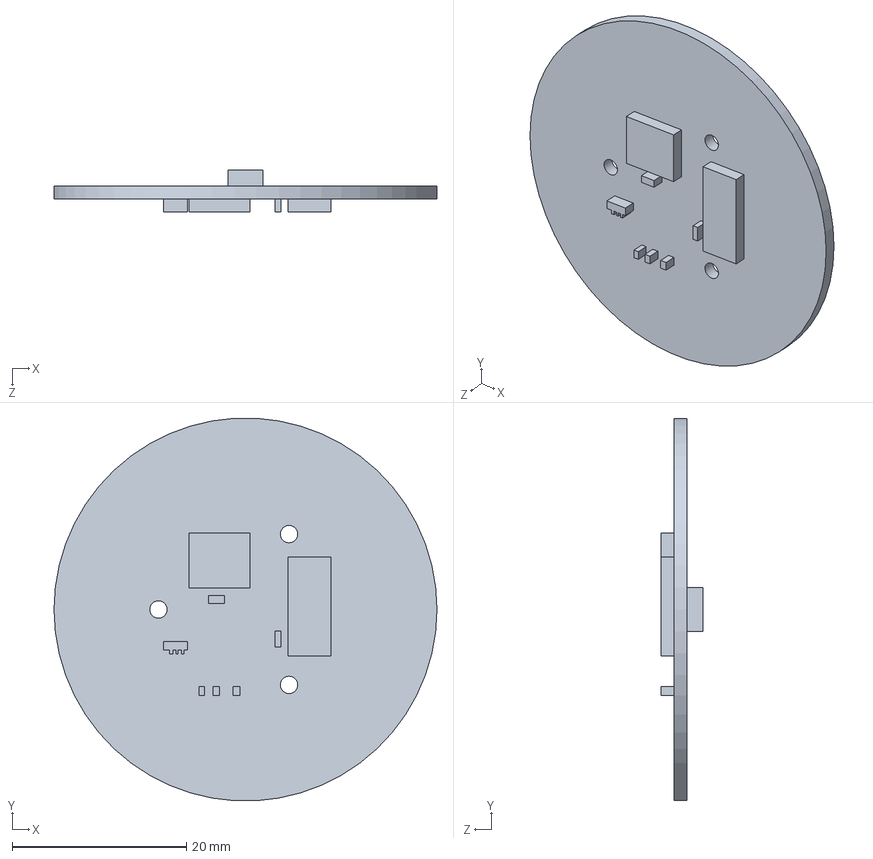
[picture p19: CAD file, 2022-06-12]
3.Model/Super Knob/pcb_main.SLDPRT
44.0 x 43.9 x 4.80 mm

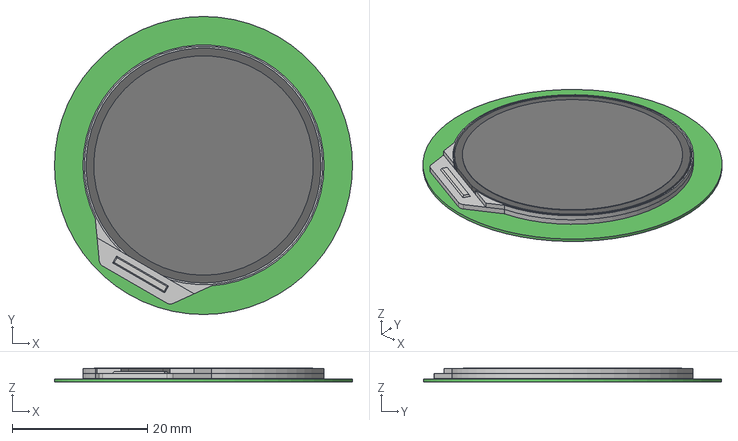
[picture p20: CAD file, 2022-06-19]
2.Hardware/SuperKnob/Screen/Screen.step
44.0 x 44.0 x 2.05 mm
scr

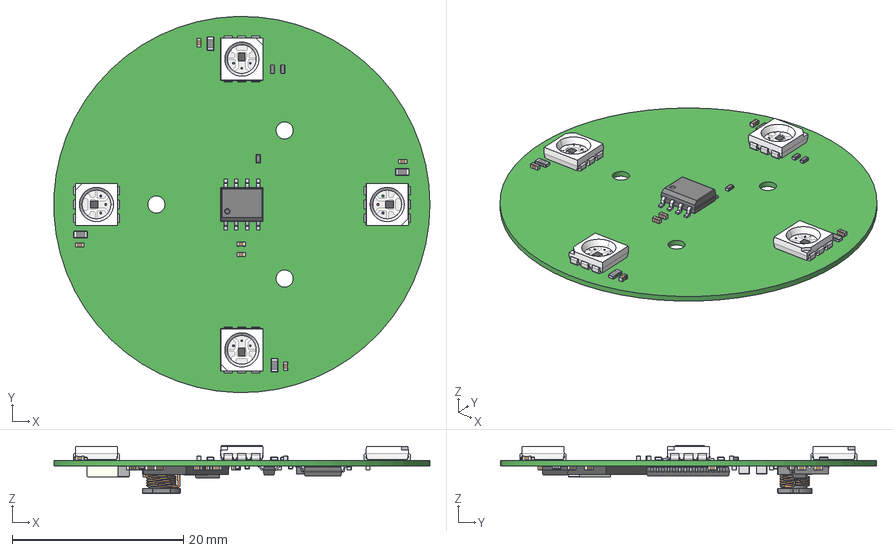
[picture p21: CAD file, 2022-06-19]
2.Hardware/SuperKnob/SuperKnob/SuperKnob.step
44.0 x 44.0 x 5.62 mm
RESC1005(0402) x 14
SOT23 x 3
CAPC1005(0402) x 23
User_Library-TSSOP-28__X2_041A043E0440043F04430441_X0_
User_Library-TSSOP-28__X2_041C04350442043A0430_X0_
User_Library-TSSOP-28__X2_041D043E0436043A0430_X0_ x 14
User_Library-mpu-6050_qfn-24
Extruded
SOT23-6
User_Library-SOIC-8_SOIC-8_Body_1
User_Library-SOIC-8_SOIC-8_Pins_1
RESC1608(0603) x 4
User_Library-WS2812S_ x 4
Inductor-CD-43
CAPC2012(0805) x 4

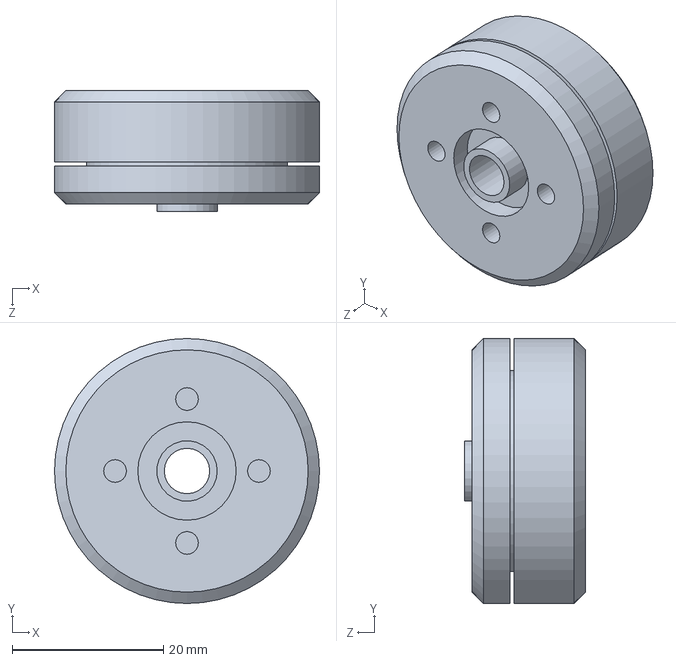
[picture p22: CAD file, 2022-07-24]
3.Model/Super Knob/motor2804.SLDPRT
35.0 x 35.0 x 16.0 mm

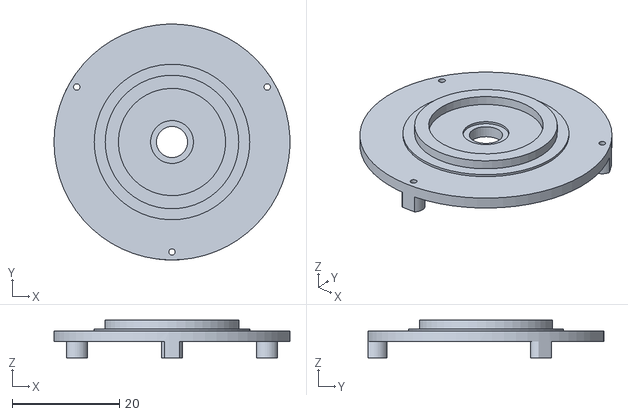
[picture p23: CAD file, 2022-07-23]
3.Model/Super Knob/STL(2804)/lcd_pcb_support.STL
44.0 x 44.0 x 7.00

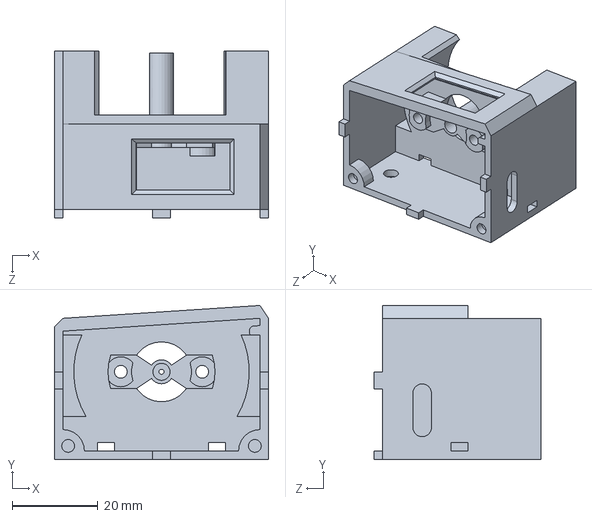
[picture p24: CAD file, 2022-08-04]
3.Model/Super Knob Lite/lite_shell_cp.SLDPRT
50.0 x 36.0 x 39.0 mm

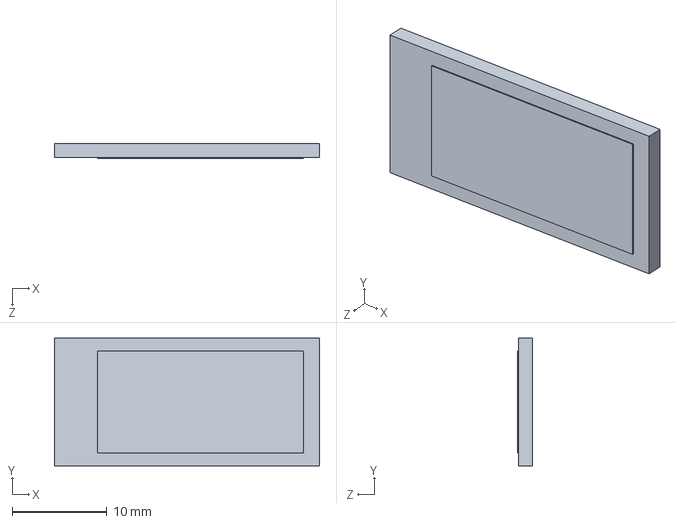
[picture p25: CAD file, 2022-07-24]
3.Model/Super Knob/LCD_ST7735.SLDPRT
28.0 x 13.5 x 1.60 mm

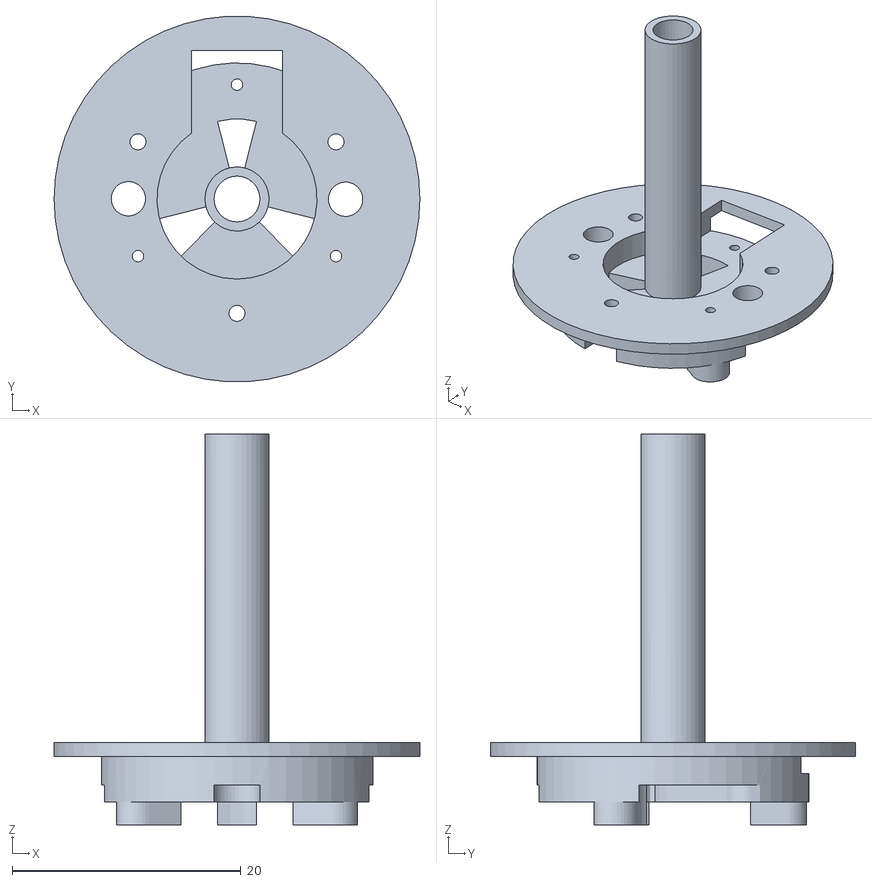
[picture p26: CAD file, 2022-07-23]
3.Model/Super Knob/STL(2804)/motor_base_2.STL
32.0 x 31.9 x 34.2

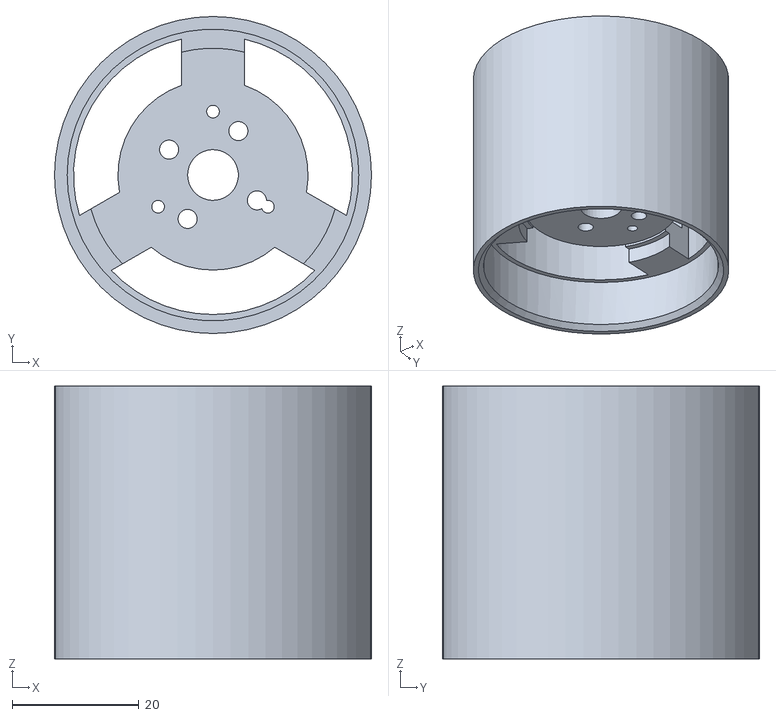
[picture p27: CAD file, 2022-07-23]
3.Model/Super Knob/STL(2804)/motor_hold_new.STL
50.0 x 50.0 x 43.0

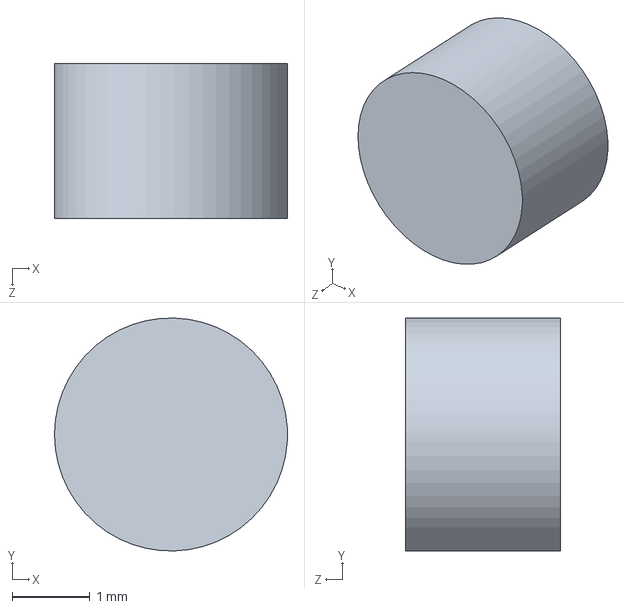
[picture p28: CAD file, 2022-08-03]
3.Model/Super Knob Lite/magnet3_2.SLDPRT
3.00 x 3.00 x 2.00 mm

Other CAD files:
3.Model/Super Knob/SuperKnob_PCB.SLDASM
3.Model/Super Knob Lite/lite_shell.SLDPRT
3.Model/Super Knob/motor_hold_new.SLDPRT
3.Model/Super Knob/STL(2804)/swan.STL
3.Model/Super Knob Lite/1元硬币.SLDPRT
3.Model/Super Knob Lite/STL/lite_shell.STL
3.Model/Super Knob Lite/Screen_st7735.SLDPRT
3.Model/Super Knob Lite/Screen_st77352.SLDPRT
3.Model/Super Knob Lite/lite_shell.STL
3.Model/Super Knob Lite/lite_shell_right.DXF
3.Model/Super Knob Lite/lite_shell_right.SLDDRW
3.Model/Super Knob Lite/lite_shell_right.SLDPRT
3.Model/Super Knob Lite/motor2804.SLDPRT
3.Model/Super Knob Lite/pcb_lcd.DXF
3.Model/Super Knob Lite/pcb_lcd_st7735.DXF
3.Model/Super Knob/1元硬币.SLDPRT
3.Model/Super Knob/LCD.SLDPRT
3.Model/Super Knob/M1.4.SLDPRT
3.Model/Super Knob/M1.4x10_p.SLDPRT
3.Model/Super Knob/M1.4x6.SLDPRT
3.Model/Super Knob/PCB_FIX.SLDPRT
3.Model/Super Knob/STL(2804)/super_knod_cap.STL
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

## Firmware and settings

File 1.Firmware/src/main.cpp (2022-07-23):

/*
 * @Descripttion: 
 * @version: 
 * @Author: congsir
 * @Date: 2022-05-14 23:55:57
 * @LastEditors: wenzheng 565402462@qq.com
 * @LastEditTime: 2022-07-23 16:22:40
 */
// https://docs.simplefoc.com/bldcmotor

#include <main.h>
#include <display.h>
#include <motor.h>
#include <tuya_control.h>
#ifdef ENABLE_BLE_KEY_BOARD
#include <ble_keyboard.h>
#endif 
#include <ws2812_driver.h>

TaskHandle_t Task_foc_Handle;  //foc 任务
TaskHandle_t Task_lvgl_Handle; //lvgl 任务
TaskHandle_t Task_module_Handle; //子模块通讯任务
TaskHandle_t Task_ws2812_Handle; //ws2812 任务

QueueHandle_t motor_msg_Queue;  //lvgl 接收消息队列
QueueHandle_t motor_rcv_Queue;  //motor 接收消息队列
QueueHandle_t ws2812_rcv_Queue;  //ws2812 接收消息队列
QueueHandle_t iot_control_Queue;  //ws2812 接收消息队列

_knob_message LVGL_MSG;
_knob_message MOTOR_MSG;
_ws2812_message WS2812_MSG;
_iot_control_message IOT_CONTROL_MSG;


void setup()
{
    pinMode(21, OUTPUT);
    digitalWrite(21, HIGH);
    Serial.begin(115200);
    Serial1.begin(115200);
    #ifdef ENABLE_BLE_KEY_BOARD
    ble_keyboard_init();
    #endif
    motor_msg_Queue = xQueueCreate(10, sizeof(struct _knob_message *));
    motor_rcv_Queue = xQueueCreate(10, sizeof(struct _knob_message *));
    ws2812_rcv_Queue = xQueueCreate(10, sizeof(_ws2812_message *));
    iot_control_Queue = xQueueCreate(10, sizeof(_ws2812_message *));

    WS2812_init();
    
    #ifdef ESP32C3_ENABLE
        xTaskCreate(Task_foc, "Task_foc", 4096, NULL, 2, &Task_foc_Handle);
        xTaskCreate(Task_lvgl, "Task_lvgl", 4096, NULL, 3, &Task_lvgl_Handle);
        xTaskCreate(Task_module, "Task_knob", 2048, NULL, 4, &Task_module_Handle);
        xTaskCreate(Task_ws2812, "Task_ws2812", 1024, NULL, 4, &Task_ws2812_Handle);
    #else
        xTaskCreatePinnedToCore(
            Task_foc, "Task_foc", 4096, NULL, 2, &Task_foc_Handle, ESP32_RUNNING_CORE);
        xTaskCreatePinnedToCore(
            Task_lvgl, "Task_lvgl", 4096, NULL, 3, &Task_lvgl_Handle, LVGL_RUNNING_CORE);
        xTaskCreatePinnedToCore(
            Task_module, "Task_knob", 2048, NULL, 4, &Task_module_Handle, ESP32_RUNNING_CORE);
        xTaskCreatePinnedToCore(
            Task_ws2812, "Task_ws2812", 1024, NULL, 4, &Task_ws2812_Handle, ESP32_RUNNING_CORE);
    #endif
}

void loop()
{
    delay(10000);
}

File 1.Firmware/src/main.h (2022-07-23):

/*
 * @Descripttion: 
 * @version: 
 * @Author: congsir
 * @Date: 2022-05-15 17:02:59
 * @LastEditors: wenzheng 565402462@qq.com
 * @LastEditTime: 2022-07-24 00:13:30
 */
#pragma once

#include <Arduino.h>

#define ENABLE_BLE_KEY_BOARD
#define ENABLE_WS2812_LED
//#define ESP32C3_ENABLE


#define LVGL_RUNNING_CORE   0            //内核选择   LVGL用核心0  其他用核心1
#define ESP32_RUNNING_CORE  1            //内核选择   LVGL用核心0  其他用核心1
#define ESP32_TOUCH_PIN1    33           //
#define ESP32_TOUCH_PIN2    32           //
#define ESP32_TOUCH_PIN3    12           //
#define WS2812_PIN          11           //定义选择引脚
#define WS2812_NUM          4            //定义led个数，决定数组长度

struct _knob_message
{
    int ucMessageID;
    char ucData[100];
};

struct _ws2812_message
{
    int ws2812_status;
    int ws2812_time;
};
struct _iot_control_message
{
    int ucMessageID;
    char ucData[100];
};

extern _knob_message LVGL_MSG;
extern _knob_message MOTOR_MSG;
extern _ws2812_message WS2812_MSG;
extern _iot_control_message IOT_CONTROL_MSG;

extern QueueHandle_t motor_msg_Queue;  //lvgl 接收消息队列
extern QueueHandle_t motor_rcv_Queue;  //motor 接收消息队列
extern QueueHandle_t ws2812_rcv_Queue;  //ws2812 接收消息队列
extern QueueHandle_t iot_control_Queue;  //ws2812 接收消息队列

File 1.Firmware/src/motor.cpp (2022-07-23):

/*
 * @Descripttion:
 * @version:
 * @Author: congsir
 * @Date: 2022-05-22 05:30:09
 * @LastEditors: wenzheng 565402462@qq.com
 * @LastEditTime: 2022-07-23 13:38:50
 */
#include <motor.h>
#include <main.h>
#include <SimpleFOC.h>
#include <display.h>
#include <ble_keyboard.h>

static KnobConfig super_knob_configs[] = {
    {
        0,
        0,
        10 * PI / 180,
        0,
        1,
        1.1,
        "Unbounded\nNo detents", //无限制  不制动
    },
    {
        32,
        0,
        8.225806452 * PI / 180,
        2,
        1,
        1.1,
        "Coarse values\nStrong detents", //粗糙的棘轮 强阻尼
    },
    {
        256,
        127,
        1 * PI / 180,
        1,
        1,
        1.1,
        "Fine values\nWith detents", //任意运动的控制  有阻尼 类似于机械旋钮
    },
    {
        256,
        127,
        1 * PI / 180,
        0,
        1,
        1.1,
        "Fine values\nNo detents", //任意运动的控制  无阻尼
    },
    {
        2, //可以运动的个数
        0,
        60 * PI / 180, //每一步60度
        1,             //制动强度为1
        1,
        0.55,                    // Note the snap point is slightly past the midpoint (0.5); compare to normal detents which use a snap point *past* the next value (i.e. > 1)
        "On/off\nStrong detent", //模拟开关  强制动
    },
};

//死区制动百分率
static const float DEAD_ZONE_DETENT_PERCENT = 0.2;
//死区RAD?
static const float DEAD_ZONE_RAD = 1 * _PI / 180;

//怠速速度ewma alpha
static const float IDLE_VELOCITY_EWMA_ALPHA = 0.001;
//怠速速度每秒钟弧度
static const float IDLE_VELOCITY_RAD_PER_SEC = 0.05;
//怠速修正延迟millis
static const uint32_t IDLE_CORRECTION_DELAY_MILLIS = 500;
//怠速校正最大角度rad
static const float IDLE_CORRECTION_MAX_ANGLE_RAD = 5 * PI / 180;
//怠速修正率
static const float IDLE_CORRECTION_RATE_ALPHA = 0.0005;

//先设置一个默认值，等消息队列发送状态过来
KnobConfig motor_config = {
    .num_positions = 32,
    .position = 0,
    .position_width_radians = 8.225806452 * _PI / 180,
    .detent_strength_unit = 2.3,
    .endstop_strength_unit = 1,
    .snap_point = 1.1,
};

//设置位置传感器（编码器、磁传感器、霍尔传感器）
// MagneticSensorI2C sensor = MagneticSensorI2C(0x36, 12, 0x0E, 4);
MagneticSensorI2C sensor = MagneticSensorI2C(AS5600_I2C);
TwoWire I2Cone = TwoWire(0);
//设置电机(极对数)
BLDCMotor motor = BLDCMotor(7);
//设置驱动器 （无刷直流电机、步进电机）
// BLDCDriver3PWM( pin_pwmA, pin_pwmB, pin_pwmC, enable使能引脚（可选的）)
// BLDCDriver3PWM driver = BLDCDriver3PWM(26, 27, 14, 12);
BLDCDriver3PWM driver = BLDCDriver3PWM(22, 4, 5, 21);

//设置电流检测 (如果不支持、可以跳过)
//在线电流检测 InlineCurrentSense。低侧电流检测 LowsideCurrentSense。
// InlineCurrentSense current_sense = InlineCurrentSense(0.01, 50, A0, A2);

//设置控制命令接口 关闭输出 可有效防止抖动
// Commander command = Commander(Serial);
// void onMotor(char *cmd) { command.motor(&motor, cmd); }


//开机初始化角度至0
void init_angle(void)
{
    float target_angle = 0;
    target_angle = sensor.getAngle();
    float delta = volt_limit / init_smooth;
    for (int i = 0; i <= init_smooth; i++)
    {
        motor.voltage_limit = delta * i;
        motor.loopFOC();
        motor.move(target_angle);
    }
    motor.voltage_limit = volt_limit;
}

float CLAMP(const float value, const float low, const float high)
{
    return value < low ? low : (value > high ? high : value);
}

void motor_shake(int strength, int delay_time)
{
    motor.move(strength);
    for (int i = 0; i < delay_time; i++)
    {
        motor.loopFOC();
        vTaskDelay(1);
    }
    motor.move(-strength);
    for (int i = 0; i < delay_time; i++)
    {
        motor.loopFOC();
        vTaskDelay(1);
    }
}

int get_motor_position(void)
{
    return motor_config.position;
}

void update_motor_status(MOTOR_RUNNING_MODE_E motor_status)
{
    struct _knob_message *send_message;
    send_message = &MOTOR_MSG;
    send_message->ucMessageID = motor_status;
    xQueueSend(motor_msg_Queue, &send_message, (TickType_t)0);
}

void update_motor_config(int status)
{
    motor_config = super_knob_configs[status];
}

void Task_foc(void *pvParameters)
{
    (void)pvParameters;

    update_motor_status(MOTOR_INIT);
    //与I2C接线有关  设置频率
    I2Cone.begin(19, 18, 400000UL);
    //初始化传感器
    sensor.init(&I2Cone);
    //传感器与电机连接
    motor.linkSensor(&sensor);
    //设置驱动器电压
    driver.voltage_power_supply = 12;
    //驱动器初始化
    driver.init();
    //驱动器与电机连接
    motor.linkDriver(&driver);
    //传感器与电机校准参数
    motor.voltage_sensor_align = 3;
    //设置FOC调制类型
    motor.foc_modulation = FOCModulationType::SpaceVectorPWM;
    //设置控制环类型：先设置为角度控制，方便初次定位
    motor.controller = MotionControlType::angle;

    //控制环 PID控制器
    motor.PID_velocity.P = 0.08;
    motor.PID_velocity.I = 4;
    motor.PID_velocity.D = 0.0002;
    motor.LPF_velocity.Tf = 0.02; //速度低通滤波
    motor.P_angle.P = 20;         //角度P控制器
    motor.velocity_limit = 5;     //位置控制的最大速度

    //电机参数监控输出串口
    motor.useMonitoring(Serial);
    //电机初始化
    motor.init();
    //校准编码器、启用FOC
    motor.initFOC();
    update_motor_status(MOTOR_INIT_SUCCESS);
    init_angle();
    //设置控制环类型：
    motor.controller = MotionControlType::torque;
    //定义电机ID
    // command.add('M', onMotor, (char *)"motor");
    // motor.move(0);
    motor.loopFOC();
    update_motor_status(MOTOR_INIT_END);

    //当前相对位置
    float current_detent_center = 0;
    //上次空闲开始状态
    uint32_t last_idle_start = 0;
    //怠速检查速度
    float idle_check_velocity_ewma = 0;

    for (;;)
    {
        motor.loopFOC();
        //监听页面状态
        struct _knob_message *lvgl_message;
        if (xQueueReceive(motor_rcv_Queue, &(lvgl_message), (TickType_t)0))
        {
            Serial.print("motor_rcv_Queue --->");
            Serial.println(lvgl_message->ucMessageID);
            switch (lvgl_message->ucMessageID)
            {
            case CHECKOUT_PAGE:
            {
                //上次的相对位置
                current_detent_center = motor.shaft_angle;
                // motor.PID_velocity.limit = 10;

                const float derivative_lower_strength = motor_config.detent_strength_unit * 0.08;
                const float derivative_upper_strength = motor_config.detent_strength_unit * 0.02;
                const float derivative_position_width_lower = radians(3);
                const float derivative_position_width_upper = radians(8);
                const float raw = derivative_lower_strength + (derivative_upper_strength - derivative_lower_strength) / (derivative_position_width_upper - derivative_position_width_lower) * (motor_config.position_width_radians - derivative_position_width_lower);
                // CLAMP可以将随机变化的值限制在一个给定的区间[min,max]内
                motor.PID_velocity.D = CLAMP(
                    raw,
                    min(derivative_lower_strength, derivative_upper_strength),
                    max(derivative_lower_strength, derivative_upper_strength));

                //存在页面切换 就震动一下
                motor_shake(2, 2);
            }
            break;
            case BUTTON_CLICK:
                motor_shake(2, 2);
                break;
            default:
                break;
            }
        }
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

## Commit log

2022-05-22 增加库移植说明文件，优化代码结构
2022-05-23 增加滚动UI与触摸检测
2022-05-24 增加中文字符支持
2022-05-24 修改readme
2022-05-24 编辑readme增加部分说明
2022-05-25 开启双缓冲和DMA，优化帧率
2022-05-26 重构项目框架
2022-05-27 编辑初版README
2022-05-29 进行界面解耦管理
2022-05-29 优化代码架构，增加UI页面
2022-05-29 增加UI界面切换逻辑
2022-05-31 绘制电机与LCD屏三维模型
    [LCD.SLDPRT, 电机32_15.SLDPRT]
2022-06-01 绘制整体模型与装配体
    [LCD.SLDPRT, motor.SLDASM, motor_base.SLDPRT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]
2022-06-03 优化3维模型
    [1元硬币.SLDPRT, bottom.SLDPRT, cont_down.SLDPRT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]
2022-06-03 禁用FOC串口配置
2022-06-04 增加多界面触感切换与消息队列
2022-06-04 支持蓝牙键盘&解决内存问题
    [huge_partition.csv]
2022-06-04 优化主页切换的复位问题
2022-06-05 实现音乐控制界面UI
2022-06-11 完善音乐播放界面UI
2022-06-12 提交硬件原理图
    [Pedestal.PcbDoc, Pedestal.PcbLib, Pedestal.PrjPcb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]
2022-06-12 完善最终3D模型
    [LCD.SLDPRT, M1.4.SLDPRT, M1.4x10_p.SLDPRT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]
2022-06-12 SCH add IMU&LED
    [SuperKnob.SchDoc, SuperKnob.SchLib]
2022-06-13 完成所有3D文件，输出STL打印测试
    [1元硬币.SLDPRT, bottom.SLDPRT, bottom.STL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]
2022-06-13 修复模型中无刷电机接线槽问题
    [motor_base_2.SLDPRT, motor_base_2.STL, super_knod.SLDASM]
2022-06-16 PCB Layout ING
    [SuperKnob.PcbDoc, SuperKnob.PcbLib, SuperKnob.PrjPcb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]
2022-06-18 增加更多字体，增大flash
    [huge_partition.csv]
2022-06-18 更正信息
2022-06-19 主板 layout 完成
    [SuperKnob.PcbDoc, SuperKnob.PrjPcb, SuperKnob.SchDoc]
2022-06-19 add Screen layout ,updata SuperKnob layout
    [Screen.GBL, Screen.GBO, Screen.GBP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]
2022-06-19 update Screen Gerber，消除板厂不识别板框问题
    [Screen.GBL, Screen.GBO, Screen.GBP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]
2022-06-19 导入PCB三维模型，修改装配体
    [Screen.step, SuperKnob.step, SuperKnob_PCB.SLDASM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]
2022-06-22 完成2.0三维图设计，并输出STL打印
    [PCB_FIX.SLDPRT, SuperKnob_PCB.SLDASM, bottom.SLDPRT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]
2022-06-24 增加ESP8266网关子模块
2022-07-01 优化番茄时钟UI界面，完善动画效果
2022-07-02 优化震动反馈
2022-07-03 验证硬件组装完整效果，适配ESP32pico
2022-07-10 完成涂鸦云接入与联调
2022-07-23 更改模型与代码可兼容2804电机
    [SuperKnob_two_motor.SLDASM, huge_partition.csv, lcd_pcb_support.SLDPRT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]
2022-07-23 增加about页面
2022-07-24 增加ST7735屏幕支持
    [LCD_ST7735.SLDPRT, SuperKnob_two_motor.SLDASM, motor2804.SLDPRT]
2022-08-01 合并 lite模型
    [1元硬币.SLDPRT, LCD.SLDPRT, LCD_ST7735.SLDPRT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]
2022-08-01 合并lite原理图与PCB
    [Screen.GBL, Screen.GBO, Screen.GBP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]
2022-08-01 编辑readme
2022-08-01 优化readme
2022-08-03 优化3D文件，整理PCB文件(向下兼容)
    [SuperKnobLite.PrjPcb, lite_shell.SLDPRT, lite_shell.STL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]
2022-08-04 更改生产时反馈的FPC座子焊盘问题
    [SuperKnobLite.PcbLib, SuperKnobLite.SchDoc]
2022-08-04 根据嘉立创反馈修改3维模型
    [lite_shell.SLDPRT, lite_shell.STL, lite_shell_cp.SLDPRT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]
2022-08-14 增加元器件链接
